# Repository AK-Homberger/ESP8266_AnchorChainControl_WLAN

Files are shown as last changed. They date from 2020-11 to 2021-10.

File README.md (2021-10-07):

# Anchor Chain Control with WLAN

This is a port from the ESP32 repository to a ESP8266 D1 Mini which is smaller than the ESP32 Node MCU.

## Caution: This is the updated version 1.2 with changed I/O pin definitions! The PCB is also updated but untested.

This repository shows how to remotely control the anchor chain relay via WLAN from phone/tablet.
Anchor chain events from the chain sensor are measured and presented on the phone/tablet.

Just set the WLAN ssid and password according to your needs. 
Select WLAN type with setting WiFiMode_AP_STA to "0" means Acess Point, or "1" means Client with DHCP.

Also set Chain_Calibration_Value according to your sensor (e.g. 0.33. meter per event).

If working as Access Point, connect the phone/tablet to the defined AP and start "192.168.4.1" in the browser.
If working as WLAN client, check the DHCP IP address with Serial Monitor of IDE and start browser with the shown IP address.



To control the anchor chain relay just press:
- "Down" for anchor down
- "Up" for anchor up
- "Stop" for Stop
- "Reset" to reset the chain counter to zero

Features:
- Saftey stop to stop "anchor up" two events before reaching zero (can be changed in code with SAFETY_STOP).
- Safety stop if maximum chain lenght is reached (standard 40 meters, can be changed with MAX_CHAIN_LENGTH)
- Watchdog timer to stop power after 1 second inactivity of client (e.g. due to connection problems).
- Watchdog timer to detect blocking chain. Engine stops if no events are detected within 1 second for up/down command.
- Current Chain Counter is stored in nonvolatile memory. ESP can be switched off after anchoring (counter is restored after new start).
- Demo mode to check functionality without having a windlass / chain counter connected to ESP (set ENABLE_DEMO to 1).

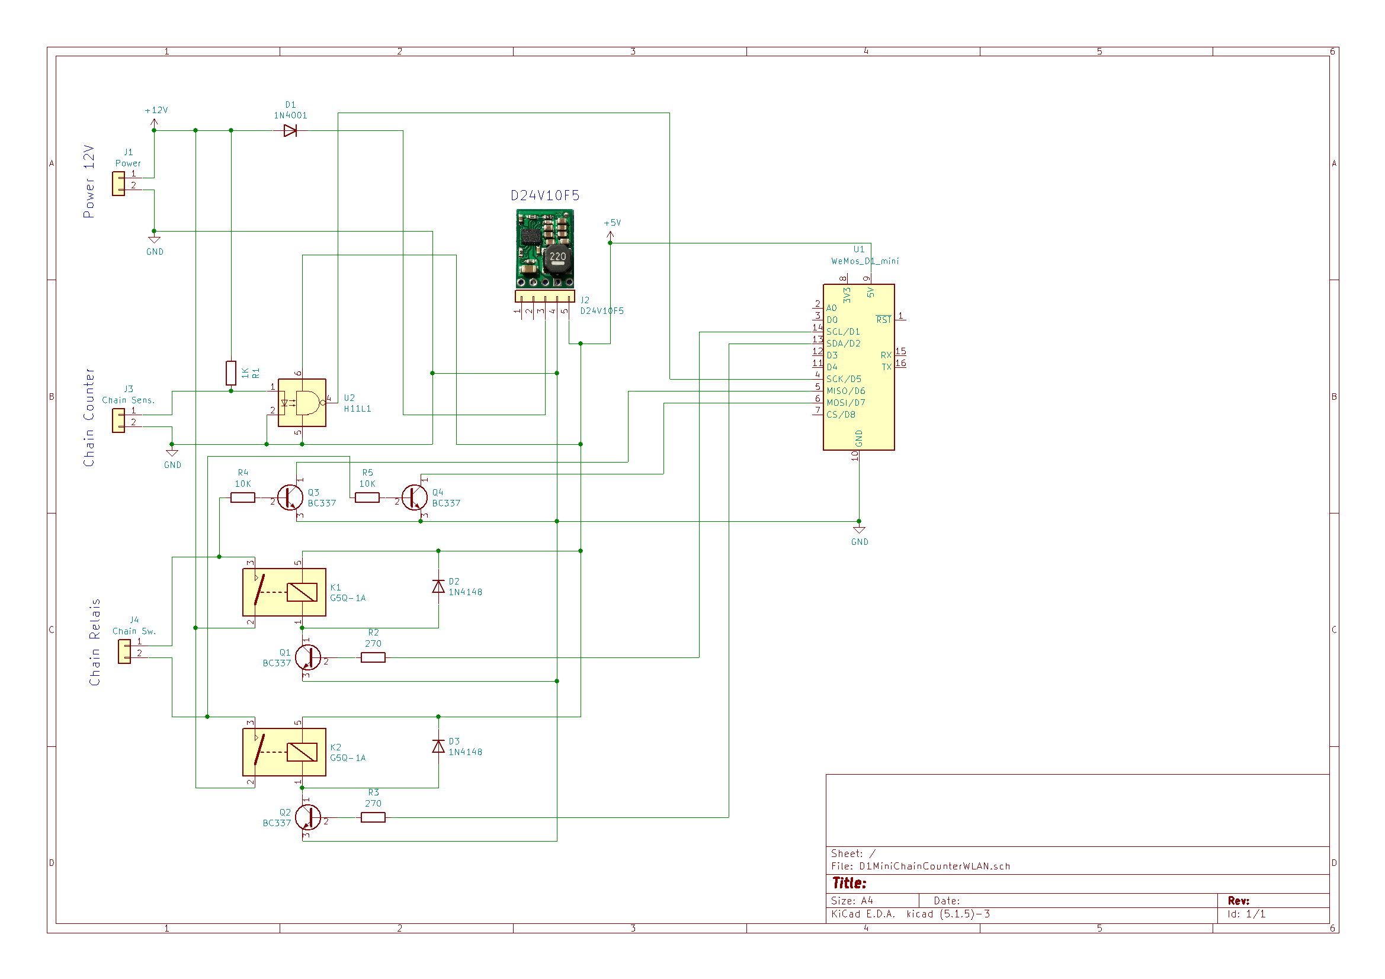
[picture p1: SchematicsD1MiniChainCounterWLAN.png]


A [pcb layout](https://github.com/AK-Homberger/ESP8266_AnchorChainContol_WLAN/blob/main/D1MiniChainCounterWLAN-Board.pdf) is available in the [KiCAD](https://github.com/AK-Homberger/ESP8266_AnchorChainControl_WLAN/tree/main/D1MiniChainCounterWLAN) folder: "D1MiniChainCounterWLAN.kicad_pcb".

You can order a PCB from Aisler.net: https://aisler.net/p/WJSHXVDM

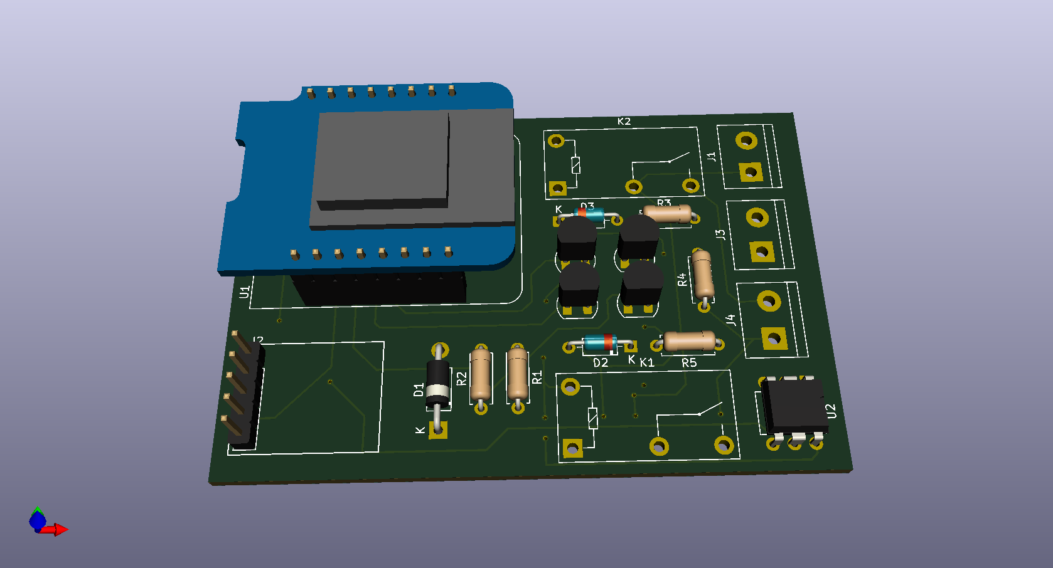
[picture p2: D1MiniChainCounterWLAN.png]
Board


The current design should work for a Quick or Lofrans anchor chain relay and chain sensor (which looks like a simple reed relay triggerd from a magnet). Connection details  for a Quick windlass/counter can be found here: https://www.quickitaly.com/resources/downloads_qne-prod/1/CHC1203_IT-EN-FR_REV001A.pdf

Used I/O pins:

- D1/D2: Output, relais Up/Down
- D6/D7: Input, manual override detection Up/Down (option)
- D5: Input, chain sensor 

With these IO pins the boot problem with the relais should be solved. Details see here: https://randomnerdtutorials.com/esp8266-pinout-reference-gpios/
The former version used D4/D5 as relais output istead of safe GPIO4(D1) and GPIO5(D2). D5,D6,D7 are safe for input.

The manual override detection function with D6/D7 is currently missing in the code. Feel free to support/update.

If you have problems with the chanin counter input measuring multiple count signals, it might be necessary to use a library to avoid multiple counts e.g.: https://github.com/mathertel/OneButton

You can easily do your own changes now: I added the full KiCAD details: https://github.com/AK-Homberger/ESP8266_AnchorChainControl_WLAN/tree/main/D1MiniChainCounterWLAN

## Parts:

- Board [Link](https://aisler.net/p/WJSHXVDM)
- U1 D1 Mini [Link](https://www.reichelt.de/de/en/d1-mini-esp8266-v3-0-d1-mini-p253978.html?&nbc=1)
- J2 D24V10F5 [Link](https://eckstein-shop.de/Pololu-5V-1A-Step-Down-Spannungsregler-D24V10F5)
- R1 Resistor 1 KOhm [Link](https://www.reichelt.de/de/en/carbon-film-resistor-1-4-w-5-1-0-kilo-ohms-1-4w-1-0k-p1315.html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)
- R2, R3 Resistor 270 Ohm (*2) [Link](https://www.reichelt.de/de/en/carbon-film-resistor-1-4-w-5-270-ohm-1-4w-270-p1390.html?&nbc=1)
- R4, R5 Resistor 10 KOhm (*2) [Link](https://www.reichelt.de/de/en/carbon-film-resistor-1-4w-5-10-kilo-ohms-1-4w-10k-p1338.html?&nbc=1)
- Q1, Q2, Q3, Q4 Transistor BC337 (*4) [Link](https://www.reichelt.de/de/en/transistor-to-92-bl-npn-45v-800ma-bc-337-25-dio-p219125.html?&nbc=1)
- D2, D3 Diode 1N4148 (*2) [Link](https://www.reichelt.de/schalt-diode-100-v-150-ma-do-35-1n-4148-p1730.html?search=1n4148)
- D1 Diode 1N4001 [Link](https://www.reichelt.de/de/en/rectifier-diode-do41-50-v-1-a-1n-4001-p1723.html?&nbc=1)
- U2 H11-L1 [Link](https://www.reichelt.de/optokoppler-1-mbit-s-dil-6-h11l1m-p219351.html?search=H11-l1)
- K1, K2 Relay (*2) [Link](https://www.reichelt.de/de/en/miniature-power-relay-g5q-1-no-5-v-dc-5-a-g5q-1a-eu-5dc-p258331.html?&nbc=1)
- J1, J3, J4 Connector 2-pin (*3) [Link](https://www.reichelt.de/de/en/2-pin-terminal-strip-spacing-5-08-akl-101-02-p36605.html?&nbc=1)

## Updates:

- 06.10.2021 - Version 1.2: Changed IO pins to avoid problem during boot and preparation for correct manual override detection.
- 06.11.2020 - Changed PCB layout to version 1.1. Larger terminal blocks (5.08 mm) and different transistor footprints for easy soldering.
- 02.11.2020 - Version 1.0: Initial version with ESP8266 D1 Mini.

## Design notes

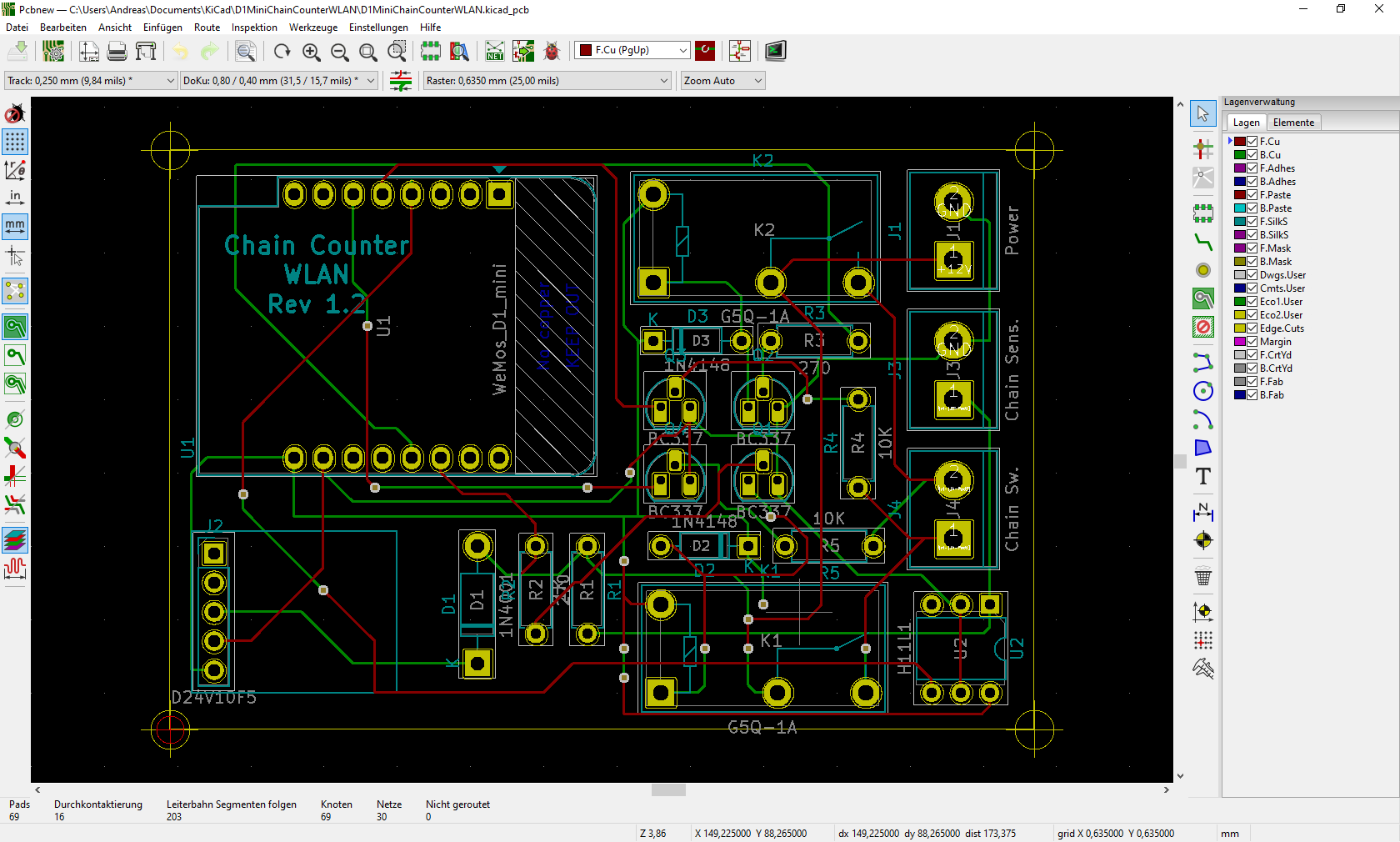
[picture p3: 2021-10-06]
D1MiniChainCounterWLAN/D1MiniChainCounterWLAN_PCB.png

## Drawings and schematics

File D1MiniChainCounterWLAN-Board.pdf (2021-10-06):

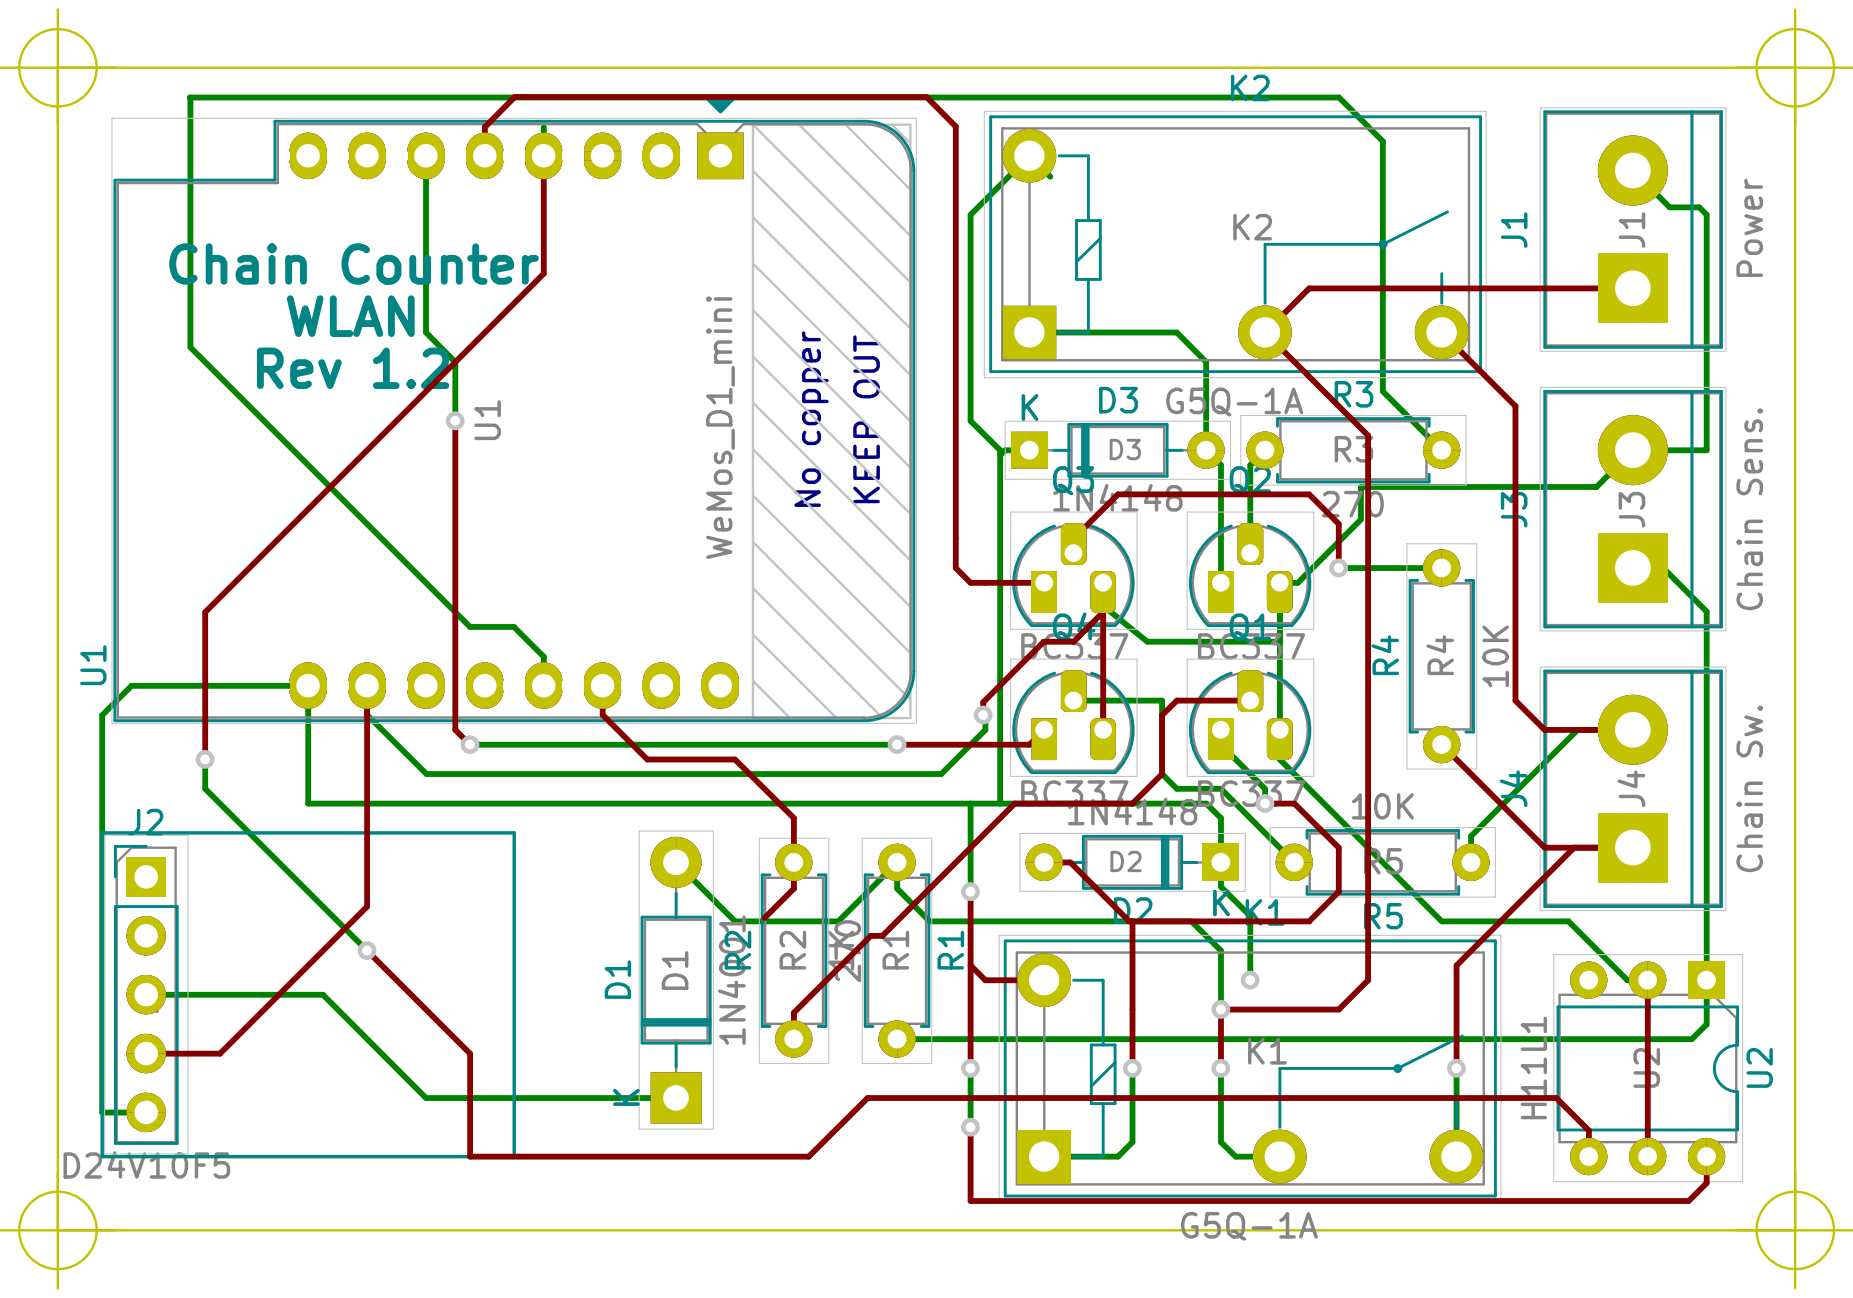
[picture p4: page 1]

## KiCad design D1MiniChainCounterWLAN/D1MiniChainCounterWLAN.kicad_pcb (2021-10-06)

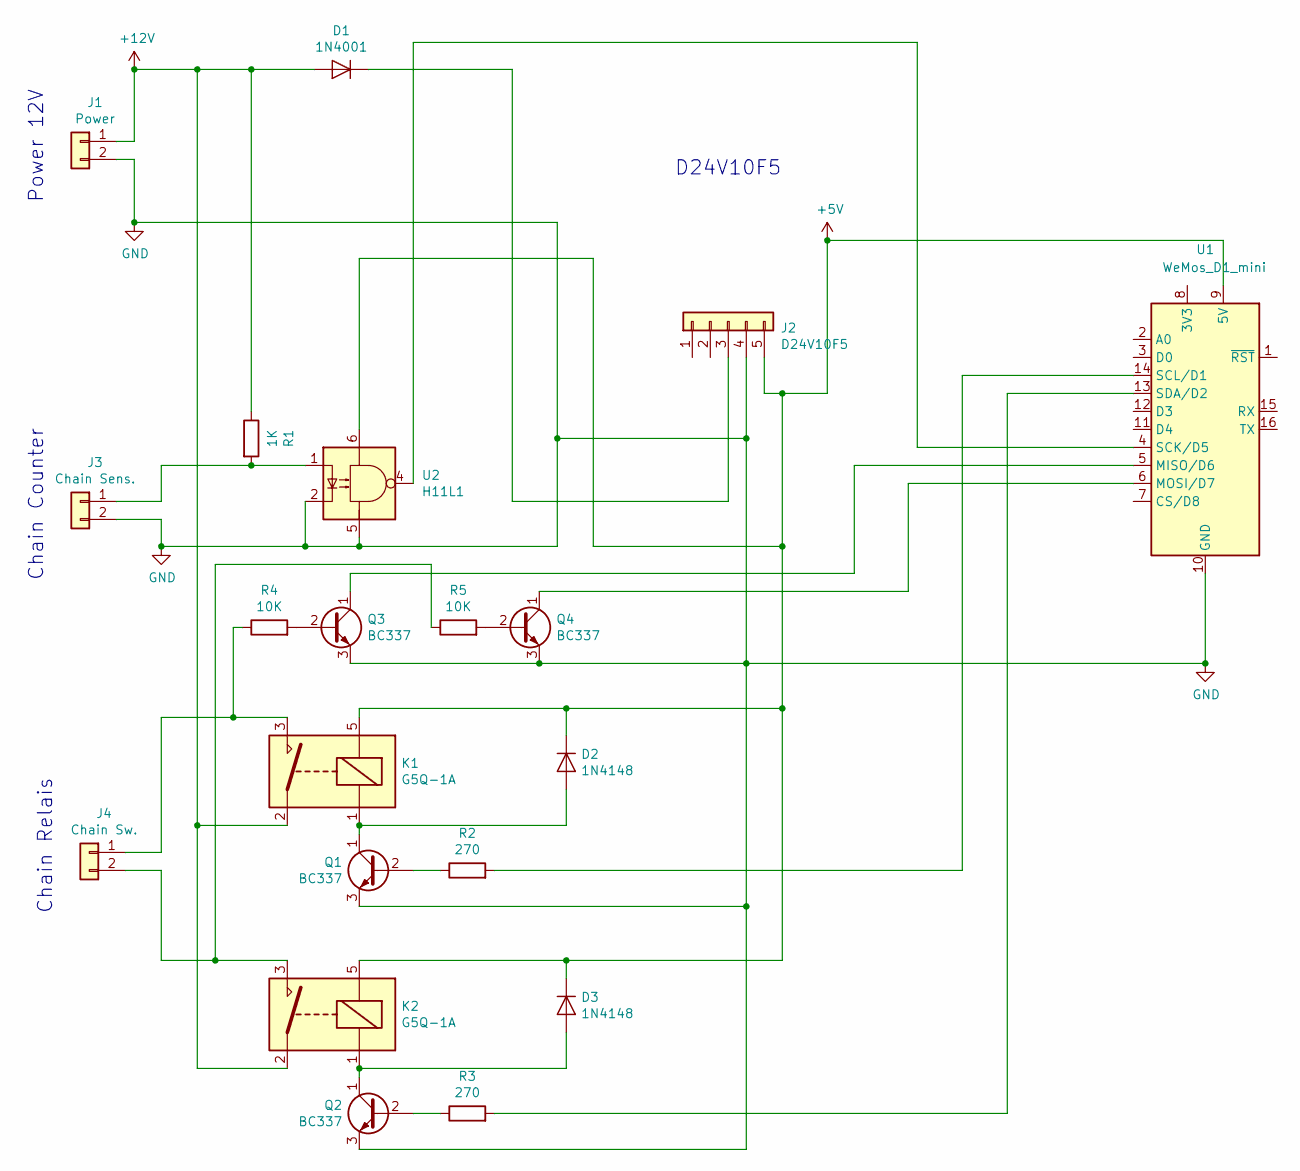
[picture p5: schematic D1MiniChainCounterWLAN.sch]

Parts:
D1: 1N4001; D_DO-41_SOD81_P10.16mm_Horizontal
D2, D3: 1N4148; D_DO-35_SOD27_P7.62mm_Horizontal
J1: Power; TerminalBlock_bornier-2_P5.08mm
J2: D24V10F5; PinHeader_1x05_P2.54mm_Vertical
J3: Chain Sens.; TerminalBlock_bornier-2_P5.08mm
J4: Chain Sw.; TerminalBlock_bornier-2_P5.08mm
K1, K2: G5Q-1A; Relay_SPST_Omron-G5Q-1A
Q1, Q2, Q3, Q4: BC337; TO-92_HandSolder
R1: 1K; R_Axial_DIN0207_L6.3mm_D2.5mm_P7.62mm_Horizontal
R2, R3: 270; R_Axial_DIN0207_L6.3mm_D2.5mm_P7.62mm_Horizontal
R4, R5: 10K; R_Axial_DIN0207_L6.3mm_D2.5mm_P7.62mm_Horizontal
U1: WeMos_D1_mini; WEMOS_D1_mini_light
U2: H11L1; DIP-6_W7.62mm

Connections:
+5V: D2.1 (K), D3.1 (K), J2.5, K1.5, K2.5, U1.9 (5V), U2.6
+12V: D1.2 (A), J1.1, K1.2, K2.2, R1.1
GND: J1.2, J2.4, J3.2, Q1.3 (E), Q2.3 (E), Q3.3 (E), Q4.3 (E), U1.10 (GND), U2.2, U2.5
unnamed: D1.1 (K), J2.3
unnamed: D2.2 (A), K1.1, Q1.1 (C)
unnamed: D3.2 (A), K2.1, Q2.1 (C)
unnamed: J3.1, R1.2, U2.1
unnamed: J4.1, K1.3, R4.1
unnamed: J4.2, K2.3, R5.1
unnamed: Q1.2 (B), R2.1
unnamed: Q2.2 (B), R3.1
unnamed: Q3.1 (C), U1.5 (MISO/D6)
unnamed: Q3.2 (B), R4.2
unnamed: Q4.1 (C), U1.6 (MOSI/D7)
unnamed: Q4.2 (B), R5.2
unnamed: R2.2, U1.14 (SCL/D1)
unnamed: R3.2, U1.13 (SDA/D2)
unnamed: U1.4 (SCK/D5), U2.4

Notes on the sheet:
D24V10F5
Chain Counter
Power 12V
Chain Relais

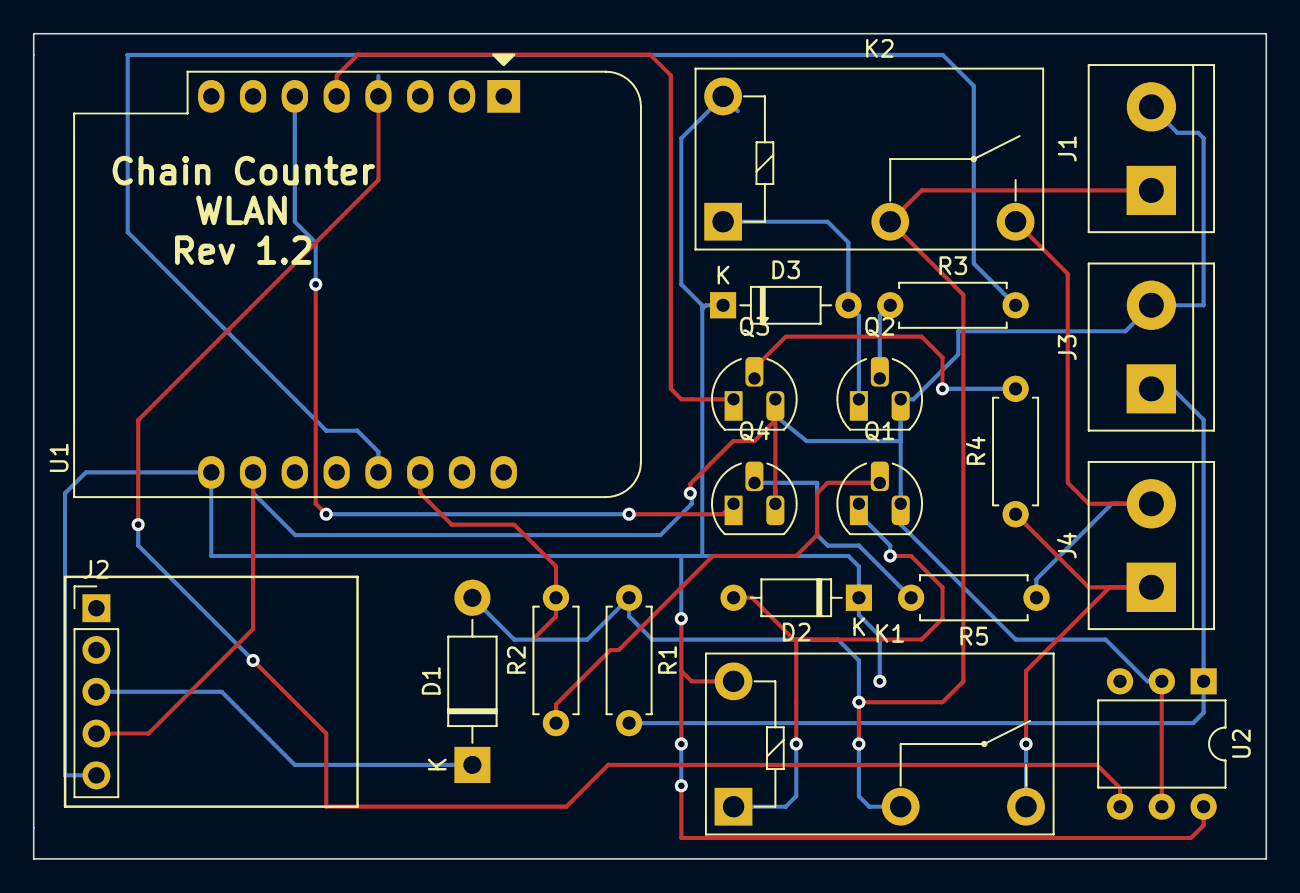
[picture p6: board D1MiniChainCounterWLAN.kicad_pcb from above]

Board: 2 copper layers, 74.9 x 50.2 mm, 20 parts (0 on the bottom side), 18 nets.

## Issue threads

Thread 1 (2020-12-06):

Manual Override

LukeSavage1306, 2020-12-06:

LukeSavage1306, 2020-12-20:
Hi AK (I’m afraid I don’t know your name - sorry!). Between myself and another UK based SignalK enthusiast we have taken your board and code and done some work on it.  This includes fixing the pin issue on the board, changing the power supply so that it can be used by boats operating at 24v as well as 12v, updating the code to track chain length when an existing control is used (or its in free fall) as well as building in a feed of chain length to SignalK. We have also done things like increasing the track width (and moving the relays to shorten the track length) for the power to the windlass relay - as some pull quite a lot of current and we thought there would be a risk of the track burning out if the windlass was operated for some time.  Given that the majority of the work is still yours would you like to pull the new version back in to your repository?  It is currently sitting on my repository (LukeSavage1306) as when I started this a couple of weeks ago I had no previous experience with GitHub and no idea how one should do these things.

Regards
Luke

jwarnes72, 2021-09-04:
Hi, I have tried to run your code on a NODEMCU DEVKIT 0.9 esp8266. Will this work? im having troubles with libraries not found and not sure what libraries i need to get the program to function. Any help greatly appreciated. cheers.

AK-Homberger, 2021-09-04:
I don’t know if the code would work. But it should in general work with any ESP8266 device. Change of used GPIO pins might be. necessary. And there are no additional libraries used.
But the PCB is for e D1 mini.

jwarnes72, 2021-09-04:
Hi. Thanks.  It does work.  Figuring out which library was missing was the tricky part,  Arduinojson and an ESP library was installed right before the errors went away. Ive changed the output pins to avoid the output relays going on during programming.  Only problem now is long term stability, which I've had with all my ESP8266 projects. Power supply and which pins to hold hi or lo via resistors is the work i need to do next.  Great code:)

LukeSavage1306, 2021-09-06:
 Hi there,  I am not an expert on this stuff.  In fact I know very little about it!  I used a D1 Mini.  I have no idea if the alternative you reference will work.   I initially followed the instructions on the AK Homberger site and got that working - then amended the code to add in the extra features (SignalK etc).  I assume it is falling over when you try to compile the programme.  If you want to send me screen shots of what is failing I will have a look and see if I can guess at what is going wrong.

Cheers
Luke

Sent from my iPhone

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

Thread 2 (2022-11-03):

Stops working

svdrummer, 2022-11-03:
Is anyone having issues where the web link just stops working and the red flasher stops?
Does the same on Android and Apply.
I am experienced with Arduino.
I am using ESP8266 D1 mini. Have used these for years.
I am using all the latest libraries and SDK
Cheers

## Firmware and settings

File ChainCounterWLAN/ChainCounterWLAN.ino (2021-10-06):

/*
  This code is free software; you can redistribute it and/or
  modify it under the terms of the GNU Lesser General Public
  License as published by the Free Software Foundation; either
  version 2.1 of the License, or (at your option) any later version.
  This code is distributed in the hope that it will be useful,
  but WITHOUT ANY WARRANTY; without even the implied warranty of
  MERCHANTABILITY or FITNESS FOR A PARTICULAR PURPOSE.  See the GNU
  Lesser General Public License for more details.
  You should have received a copy of the GNU Lesser General Public
  License along with this library; if not, write to the Free Software
  Foundation, Inc., 51 Franklin St, Fifth Floor, Boston, MA  02110-1301  USA
*/

// Anchor Chain Remote Control / Chain Counter with WLAN.
// Version 1.2, 06.10.2021, AK-Homberger

#include<ESP8266WiFi.h>
#include<ESP8266WebServer.h>
#include<EEPROM.h>

#include "index_html.h"              // Web site information for Gauge / Buttons

#define ENABLE_DEMO 1                // Set to 1 to enable Demo Mode with up/down counter
#define SAFETY_STOP 2                // Defines safety stop for chain up. Stops defined number of events before reaching zero
#define MAX_CHAIN_LENGTH 40          // Define maximum chan length. Relay off after the value is reached

// Wifi: Select AP or Client

#define WiFiMode_AP_STA 0            // Defines WiFi Mode 0 -> AP (with IP:192.168.4.1 and  1 -> Station (client with IP: via DHCP)
const char *ssid = "chaincount";     // Set WLAN name
const char *password = "kette0102";  // Set password

ESP8266WebServer server(80);                // Web Server at port 80


// Chain Counter

#define Chain_Calibration_Value 0.33 // Translates counter impuls to meter 0,33 m per pulse
#define Chain_Counter_Pin D5         // Counter impulse is measured as interrupt on pin D5
unsigned long Last_int_time = 0;     // Time of last interrupt
unsigned long Last_event_time = 0;   // Time of last event for engine watchdog
int ChainCounter = 0;                // Counter for chain events
int LastSavedCounter = 0;            // Stores last ChainCounter value to allow storage to nonvolatile storage in case of value changes

// Relay

#define Chain_Up_Pin D1              // GPIO pin D1 for Chain Up Relay
#define Chain_Down_Pin D2            // GPIO pin D2 for Chain Down Relay
int UpDown = 1;                      // 1 =  Chain down / count up, -1 = Chain up / count backwards
int OnOff = 0;                       // Relay On/Off - Off = 0, On = 1
unsigned long Watchdog_Timer = 0;    // Watchdog timer to stop relay after 1 second of inactivity e.g. connection loss to client


// Chain Event Interrupt
// Enters on falling edge

void IRAM_ATTR handleInterrupt() {
  noInterrupts();

  if (millis() > Last_int_time + 10) {  // Debouncing. No new events for 10 milliseconds

    ChainCounter += UpDown;             // Chain event: Count up/down

    if ( ( (ChainCounter <= SAFETY_STOP) && (UpDown == -1) && (OnOff == 1) ) ||     // Safety stop counter reached while chain is going up
         ( (UpDown == 1) && (abs(ChainCounter) * Chain_Calibration_Value >= MAX_CHAIN_LENGTH) ) ) {  // Maximum chain lenght reached

      digitalWrite(Chain_Up_Pin, LOW );
      digitalWrite(Chain_Down_Pin, LOW );
      OnOff = 0;
    }
    Last_event_time = millis();         // Store last event time to detect blocking chain
  }
  Last_int_time = millis();             // Store last interrupt time for debouncing
  interrupts();
}


void setup() {
  int wifi_retry = 0;

  // Relay output
  pinMode(Chain_Up_Pin, OUTPUT);            // Sets pin as output
  pinMode(Chain_Down_Pin, OUTPUT);          // Sets pin as output
  digitalWrite(Chain_Up_Pin, LOW );         // Relay off
  digitalWrite(Chain_Down_Pin, LOW );       // Relay off

  // Init Chain Count measure with interrupt
  pinMode(Chain_Counter_Pin, INPUT_PULLUP); // Sets pin input with pullup resistor
  attachInterrupt(digitalPinToInterrupt(Chain_Counter_Pin), handleInterrupt, FALLING); // Attaches pin to interrupt on falling edge

  // Init serial
  Serial.begin(115200);
  Serial.print("");
  Serial.println("Start");

  EEPROM.begin(16);
  ChainCounter = EEPROM.read(0);
  LastSavedCounter = ChainCounter;                  // Initialise last counter value

  // Init WLAN AP
  if (WiFiMode_AP_STA == 0) {

    WiFi.mode(WIFI_AP);                              // WiFi Mode Access Point
    delay (100);
    WiFi.softAP(ssid, password); // AP name and password
    Serial.println("Start WLAN AP");
    Serial.print("IP address: ");
    Serial.println(WiFi.softAPIP());

  } else {

    Serial.println("Start WLAN Client DHCP");         // WiFi Mode Client with DHCP
    WiFi.begin(ssid, password);

    while (WiFi.status() != WL_CONNECTED) {           // Check connection
      wifi_retry++;
      delay(500);
      Serial.print(".");
      if (wifi_retry > 10) {
        Serial.println("\nReboot");                   // Reboot after 10 connection tries
        ESP.restart();
      }
    }

    Serial.println("");
    Serial.println("WiFi connected");
    Serial.println("IP address: ");
    Serial.println(WiFi.localIP());
  }


  // Handle HTTP request events

  server.on("/", Event_Index);
  server.on("/gauge.min.js", Event_js);
  server.on("/ADC.txt", Event_ChainCount);
  server.on("/up", Event_Up);
  server.on("/down", Event_Down);
  server.on("/stop", Event_Stop);
  server.on("/reset", Event_Reset);

  server.onNotFound(handleNotFound);

  server.begin();
  Serial.println("HTTP Server started");
}


void Event_Up() {                          // Handle UP request
  server.send(200, "text/plain", "-1000"); // Send response "-1000" means no  chainlenght
  Serial.println("Up");
  digitalWrite(Chain_Up_Pin, HIGH );
  digitalWrite(Chain_Down_Pin, LOW );
  Last_event_time = millis();
  UpDown = -1;
  OnOff = 1;
}


void Event_Down() {                         // Handle Down request
  server.send(200, "text/plain", "-1000");  // Send response "-1000" means no  chainlenght
  Serial.println("Down");
  digitalWrite(Chain_Up_Pin, LOW );
  digitalWrite(Chain_Down_Pin, HIGH );
  Last_event_time = millis();
  UpDown = 1;
  OnOff = 1;
}


void Event_Stop() {                         // Handle Stop request
  server.send(200, "text/plain", "-1000");  // Send response "-1000" means no  chainlenght
  Serial.println("Stop");
  digitalWrite(Chain_Up_Pin, LOW );
  digitalWrite(Chain_Down_Pin, LOW );
  OnOff = 0;
}


void Event_Reset() {                        // Handle reset request to reset counter to 0
  ChainCounter = 0;
  server.send(200, "text/plain", "-1000");  // Send response "-1000" means no  chainlenght
  Serial.println("Reset");
}


void Event_Index() {                         // If "http://<ip address>/" requested
  server.send(200, "text/html", indexHTML);  // Send Index Website
}


void Event_js() {                            // If "http://<ip address>/gauge.min.js" requested
  server.send(200, "text/html", gauge);      // Then send gauge.min.js
}


void Event_ChainCount() {                    // If  "http://<ip address>/ADC.txt" requested
  
  float temp = (ChainCounter * Chain_Calibration_Value); // Chain in meters
  server.sendHeader("Cache-Control", "no-cache");
  server.send(200, "text/plain", String (temp));

  Watchdog_Timer = millis();                 // Watchdog timer is set to current uptime

#if ENABLE_DEMO == 1                         // Demo Mode - Counts automatically UP/Down every 500 ms

  if (OnOff == 1) ChainCounter += UpDown;

  if ( ( (ChainCounter <= SAFETY_STOP) && (UpDown == -1) && (OnOff == 1) ) ||     // Safety stop counter reached while chain is going up
       ( (UpDown == 1) && (abs(ChainCounter) * Chain_Calibration_Value >= MAX_CHAIN_LENGTH) ) ) {  // Maximum chain lenght reached

    digitalWrite(Chain_Up_Pin, LOW );
    digitalWrite(Chain_Down_Pin, LOW );
    OnOff = 0;
  }
  Last_event_time = millis();
#endif

}


void handleNotFound() {                                           // Unknown request. Send error 404
  server.send(404, "text/plain", "File Not Found\n\n");
}


void loop() {
  int wifi_retry = 0;

  server.handleClient();                                           // Handle HTTP requests

  if ( ( millis() > Watchdog_Timer + 1000 ) ||                     // Check HTTP connnection
       ( (OnOff == 1) && (millis() > Last_event_time + 1000)) )  { // Check events if engine is on

    digitalWrite(Chain_Up_Pin, LOW );                              // Relay off after 1 second inactivity
    digitalWrite(Chain_Down_Pin, LOW );
    OnOff = 0;
  }

  if (ChainCounter != LastSavedCounter) {                          // Store Chain Counter to nonvolatile storage (if changed)
    EEPROM.write(0, ChainCounter);
    EEPROM.commit();
    LastSavedCounter = ChainCounter;
  }

  if (WiFiMode_AP_STA == 1) {                                      // Check connection if working as client
    while (WiFi.status() != WL_CONNECTED && wifi_retry < 5 ) {     // Connection lost, 5 tries to reconnect
      wifi_retry++;
      Serial.println("WiFi not connected. Try to reconnect");
      WiFi.disconnect();
      WiFi.mode(WIFI_OFF);
      WiFi.mode(WIFI_STA);
      WiFi.begin(ssid, password);
      delay(100);
    }
    if (wifi_retry >= 5) {
      Serial.println("\nReboot");                                  // Did not work -> restart ESP32
      ESP.restart();
    }
  }

  // Dummy to empty input buffer to avoid board to stuck with e.g. NMEA Reader
  if ( Serial.available() ) {
    Serial.read();
  }
}

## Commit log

2020-11-06 Version 1.1
    [D1MiniChainCounterWLAN.kicad_pcb]
2021-10-06 KiCAD Version 1.2 files
    [D1MiniChainCounterWLAN.kicad_pcb, D1MiniChainCounterWLAN.sch]
